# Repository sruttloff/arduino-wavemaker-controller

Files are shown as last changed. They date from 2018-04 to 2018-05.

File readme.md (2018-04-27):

2 Jebao Wavemaker (SW-4) Pumpen selbst steuern
=======
Da das Strömungsbild trotz der vielen Möglichkeiten die die Controller von Hause aus bieten, nicht meinen Wünschen entsprach, habe ich dieses kleine Projekt auf die Beine gestellt.
Über die PWM Pins des Arduino wird ein Signal erzeugt und mit einem RC-Glied in eine Gleichspannung umgewandelt.
Die Gleichspannung wird über den OP verstärkt und liefert am OP Ausgang 0-9V (oder 0-10V wenn man eine 10V Spannungsquelle hat).
Im Programm wird Pump1 als Master betrachtet und Pumpe 2 ist Slave. Wenn Pump1 auf 100% läuft, läuft Pumpe2 mit 0%.
Es gibt 4 Timings (siehe Bild) die man frei definieren kann. Auch sind 0% und 100% Leistung frei einstellbar (PWM Rate 0-255).
0% bedeutet bei mir, dass die Pumpe mit minimaler Leistung läuft, so dass diese gerade nicht stehen bleibt.
Den Arduino Sketch also einfach im Kopfteil an die eigenen Bedürfnisse anpassen.

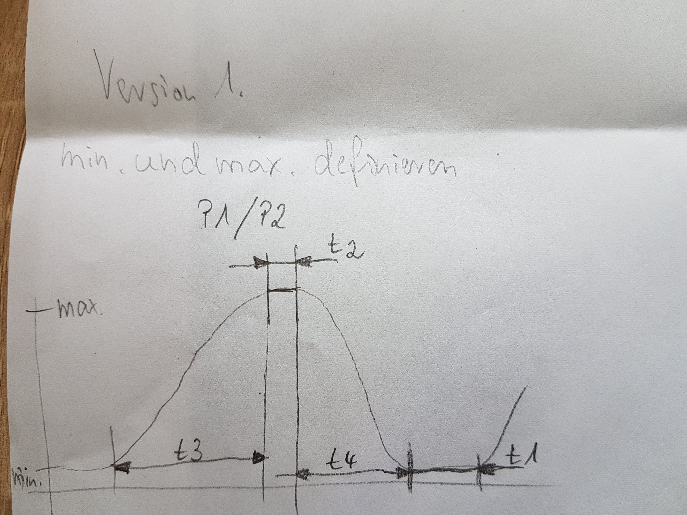
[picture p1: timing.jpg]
Timing Diagramm


Zur Umsetzung benötigt wird:
1. Arduino Mega 2560 (eine kleinere Version des Arduino tut's auch, dann muss allerdings die Pinbelegung angepasst werden)
2. 1 x OP Verstärker LM358
3. 6 x 10kOhm Widerstände
4. 2 x 22uF Elko's
5. Netzteil mit 9-12V DC
6. Ein paar Meter 2 Adriges Kabel + Hohlstecker (3,5mm / 1,45mm) um die Controller der Pumpen anzuschliessen.

Hier der Schaltplan:
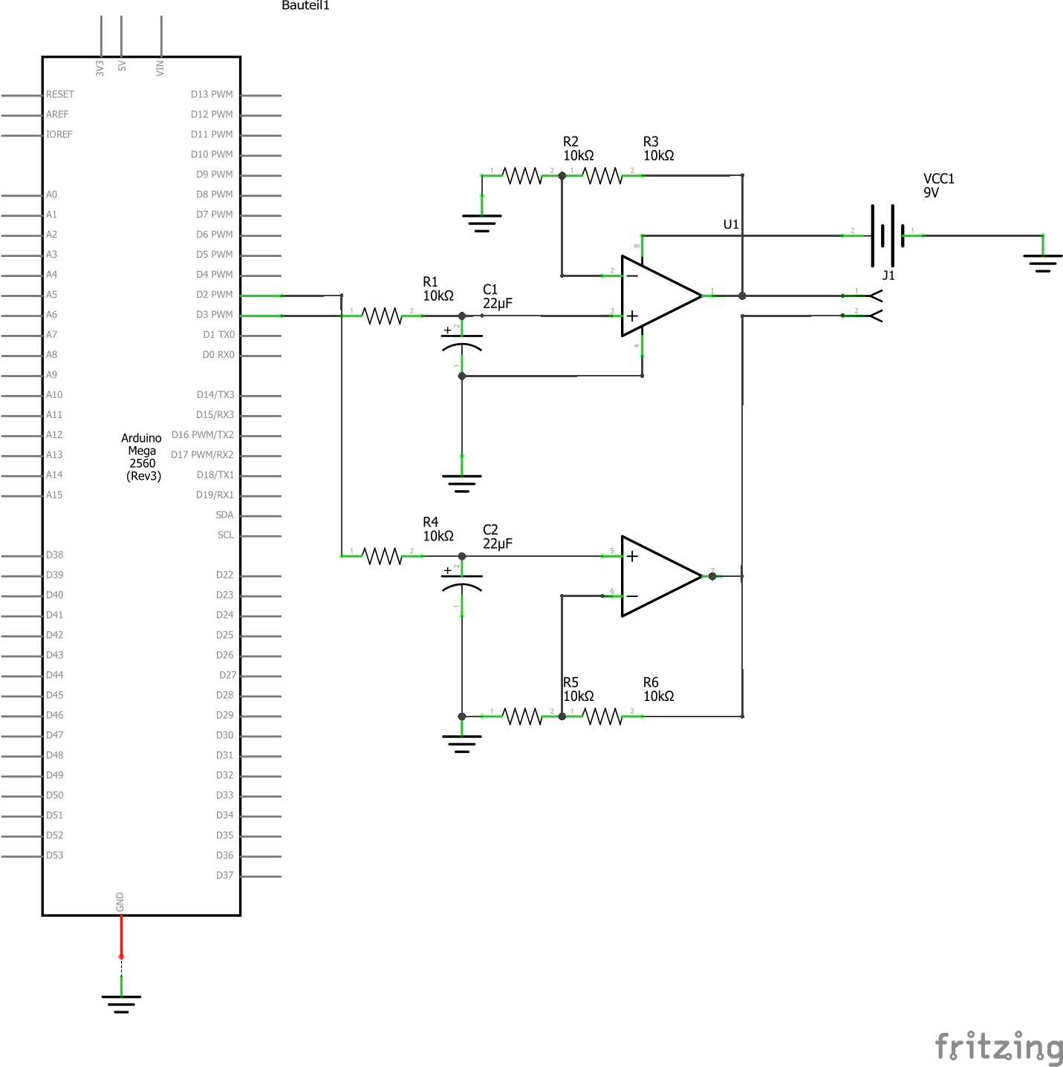
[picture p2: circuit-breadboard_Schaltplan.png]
Schaltplan


Hier der Aufbau auf einer Steckplatine (Breadboard):
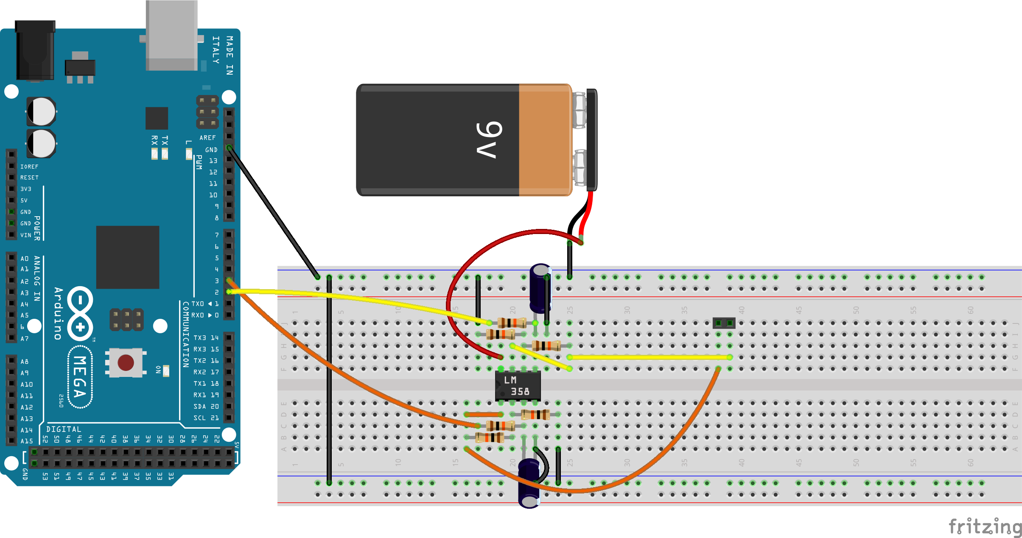
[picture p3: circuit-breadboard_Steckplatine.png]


Die Pin 1 und 2 von J1 liefern dann die Spannung von 0-9V für die beiden Controller.
Ich selbst habe die SW-4 Controller mit Hohlsteckern angeschlossen.
Hat man die Version der Controller ohne die Steckanschlüsse, muss man das Gehäuse öffnen. Einfach die 4 Schrauben auf der Rückseite entfernen.
Dann den Deckel abnehmen. Nun muss die Platine gelöst werden. An der Stelle wo eigentlich die Buchse sitzen sollte, wurde vom Hersteller der Ground-Pin mit dem Kontaktpin der Buchse verlötet.
Entweder ist da nur sehr viel Lötzinn drauf oder ein Draht wurde zwischengelötet. Das muss man entfernen.
Der Nachteil ist hierbei, dass der Controller nun nichts mehr tut, da er auf ein Signal von aussen wartet. 
Einen Kippschalter aufzulöten, bringt die Lösung. So kann man zwischen normalem und externem Modus umschalten.

Hier ein Foto wo man den Draht anlötet:
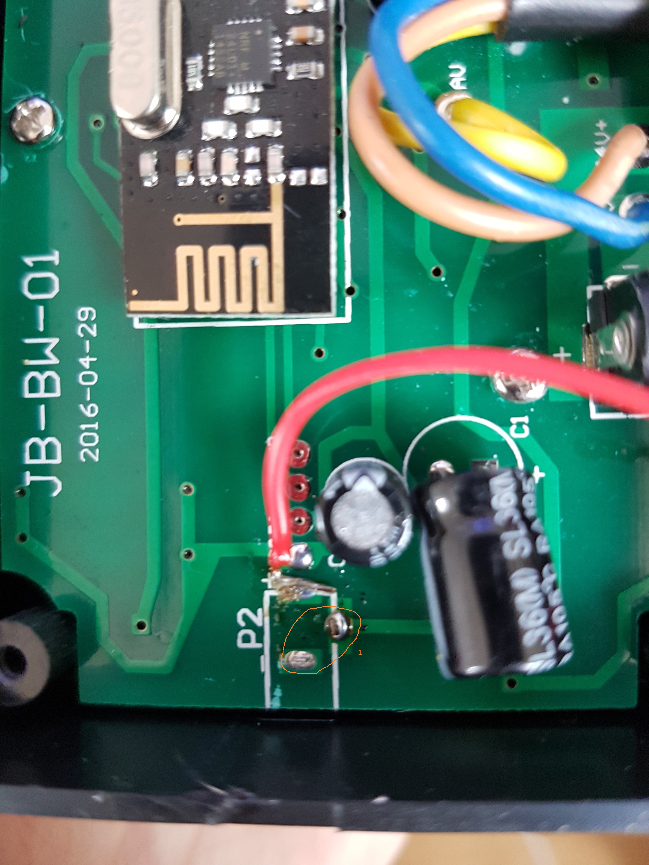
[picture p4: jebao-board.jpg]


Markierung 1 zeigt, wo die Brücke auf der Vorderseite der Platine zu entfernen ist. Statt der Brücke einen Schalter zwischen setzen.
An den - kommt dann der Minus von der Schaltung und an + der Ausgang von der Schaltung.

Optionaler Schalter zur Fütterung
Bei Drücken des Schalters wird der Fütterungsmodus aktiviert. Die Pumpen stehen für 10 Sekunden still.
Erneutes Drücken, bricht den Modus ab.
Hier der Schaltplan und der Aufbau auf einer Steckplatine (Breadboard)::
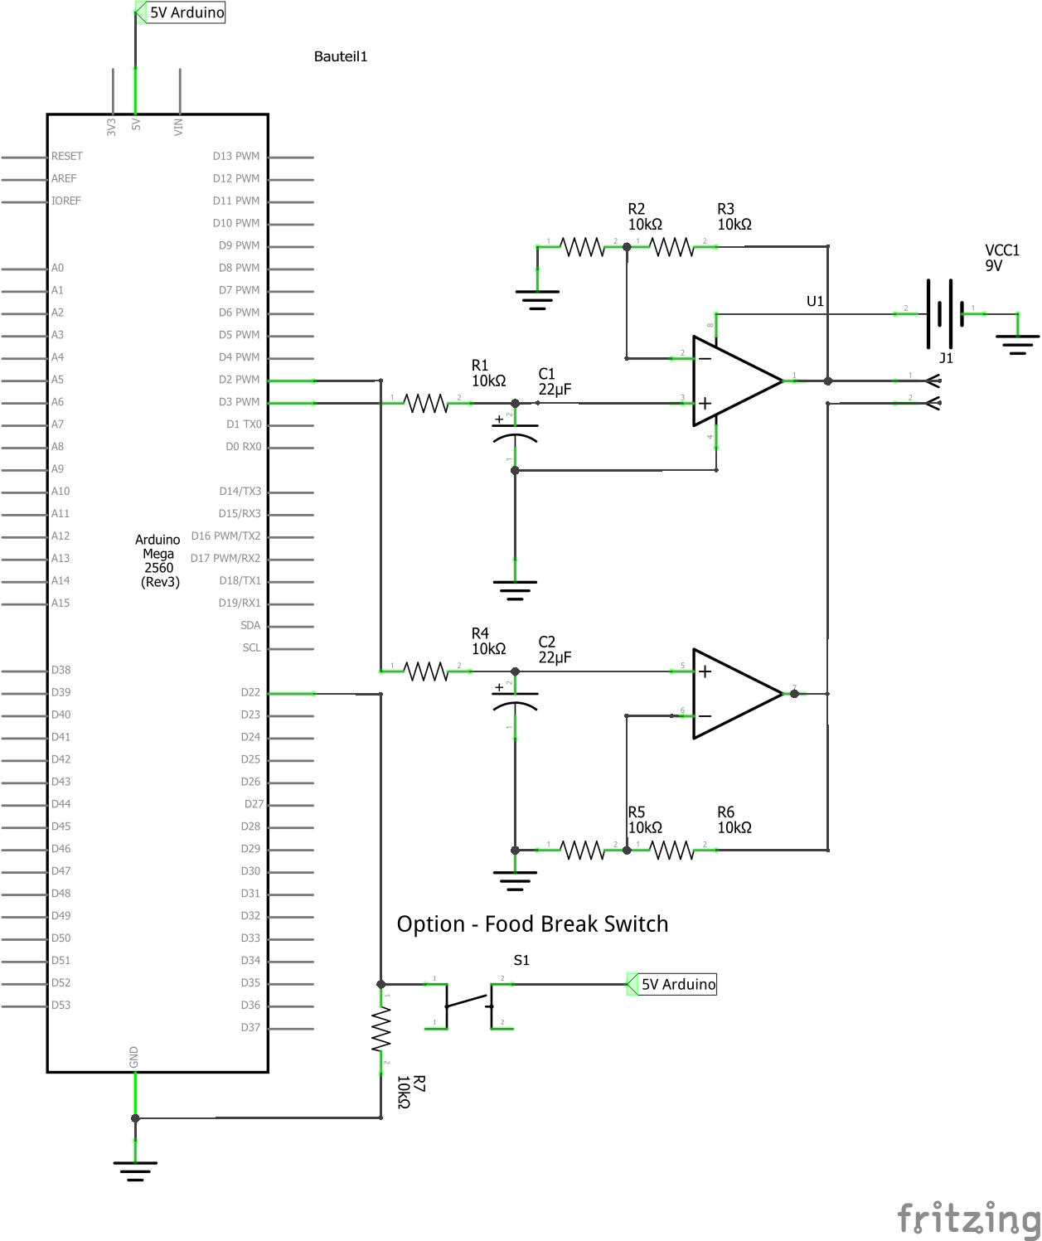
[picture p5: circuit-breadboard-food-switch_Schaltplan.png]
Schaltplan


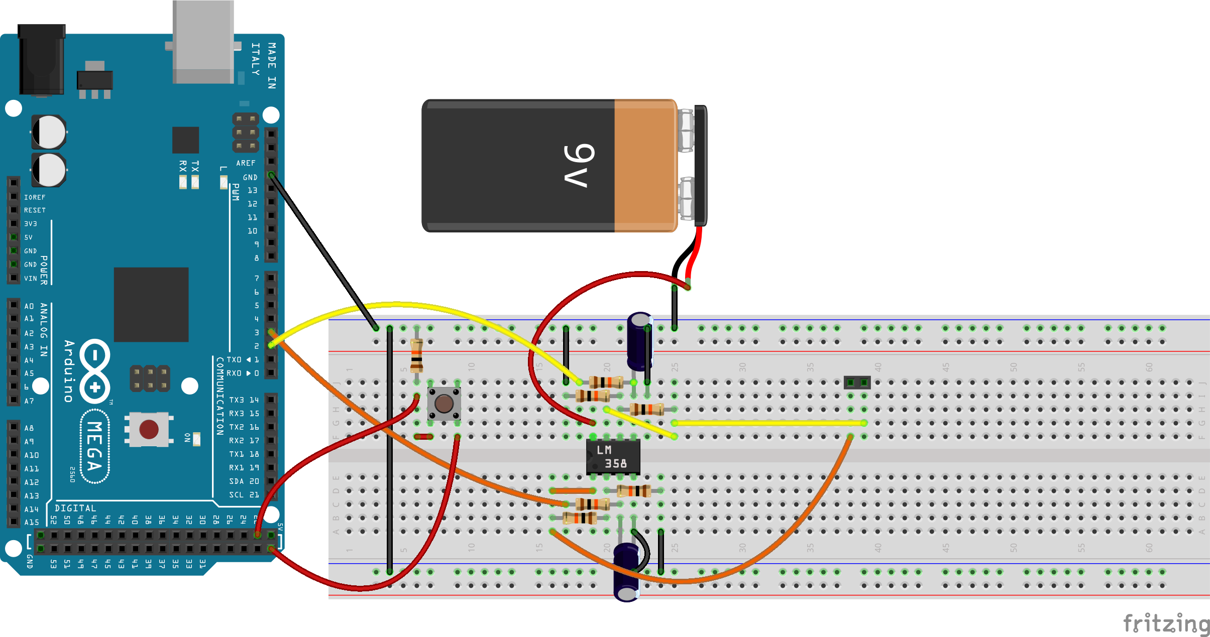
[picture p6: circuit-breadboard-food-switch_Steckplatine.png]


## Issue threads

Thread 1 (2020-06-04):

nRF24 protocol

martinhladil, 2020-06-04:
Very nice project to control the pump in an analog way. Thanks for that!

However, have you ever thought about controlling it via nRF24 which is on board? This is the way how master controller speaks to slave controllers wirelessly. I'm thinking about cracking it by myself, I'm just curious if you maybe did some progress here as well.

sruttloff, 2020-06-04:
Thank you for your interest.
No, I did not want to implement this via the slave function (radio). Quite simply to be able to use other controllers with 10V input at a later time.
The Jebao pumps have now also been replaced and it was sufficient to produce a suitable cable.

Closed 2020-06-04.

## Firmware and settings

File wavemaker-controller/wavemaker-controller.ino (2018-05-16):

/*
  Jebao SW Wavemaker Controller with Arduino Mega

  Does controll 2 Wavemaker controller (0-10V DC). One is master, the other is slave and runs reversed against No.1
  Food Button can be connected optionally.  

  Free for all!
 */

#include <Arduino.h>
extern HardwareSerial Serial;

int pump1 = 3; // the PWM pin the right pump is attached to
int pump2 = 4; // the PWM pin the left pump is attached to
int pump1Min = 45; //45 ist der kleinste
int pump1Max = 235;
int pump2Min = 45;
int pump2Max = 255;
int pump1Current = 0, pump2Current = 0;
int t1 = 30; // time in secs. to stay at level min
int t2 = 30; // time in secs. to stay at max
int t3 = 15; // time in secs. to go from min to max
int t4 = 15; // time in secs. to go from max to min

/*
 * timer 1 = for wavemaker timing
 * timer 5 = food timer
 */
const int timerElements = 5; // qty of timer's to init
unsigned long timerArray[timerElements + 1];
unsigned long tempTime[timerElements + 1]; // needed to calculate progress
String step = "t1"; // step marker
float myTimer(int timerNo = 0, long time = 0);
void setPump1Speed(float rate);
void setPump2Speed(float rate);
void pumpMaster();
int foodBreak = 0;
long foodTime = 600; // food time in secs.
int foodSwitch = 22;
int tmpSwitch = 0;
float tmpFood = 0;

void setup() {
    pinMode(pump1, pump1Current);
    pinMode(pump2, pump2Current);
    Serial.begin(9600);
    // init timer array  
    for (int i = 0; i < timerElements; i++) {
        timerArray[i] = 0;
        tempTime[i] = 0;
    }
    pinMode(foodSwitch, INPUT);
    digitalWrite(foodSwitch, HIGH);
    setPump1Speed(50.0);
    delay(500);
}

void foodSwitchAction() {
    int digitalVal = digitalRead(foodSwitch);
    // switch pressed
    if (!tmpSwitch && HIGH == digitalVal)
        tmpSwitch = 1;
    // switch released
    if (tmpSwitch && LOW == digitalVal) {
        tmpSwitch = 0;
        if (foodBreak == 1) {
            // make timer run out of time
            Serial.println("Switch Pressed and released to stop timer");
            myTimer(5, (long) 1);
        } else {
            foodBreak = 1;
            analogWrite(pump1, 0);
            analogWrite(pump2, 0);
            // start food timer
            foodTime = (long) foodTime * (long) 1000;
            Serial.println("Switch Pressed and released " + String(foodTime));
            myTimer(5, (long) foodTime);
        }
    }
    if (foodBreak == 1) {
        float tmp = myTimer(5);
        if (tmpFood < tmp) {
            tmpFood = ceil(tmp);
            Serial.println("Food Timer at " + String(tmpFood) + "%");
        }
        // timer reached      
        if (tmp >= 100.00) {
            foodBreak = pump1Current = pump2Current = 0;
            step = "t1";
            myTimer(5, -1); // reset Timer
            myTimer(1, -1); // reset pump Timer
            setPump1Speed(50.0);
            delay(700);
            Serial.println("Food end");
        }
    }
}

void loop() {
    if (!foodBreak)
        pumpMaster();
    foodSwitchAction();
    test();
}
void setPump1Speed(float rate) {
    // rate is percent
    int tmpRange = pump1Max - pump1Min;
    if (rate < 0.00)
        rate = 0.00;
    if (rate > 100.00)
        rate = 100.00;
    int speed = (float) pump1Min + (tmpRange * (rate / 100.00));
    // set new speed when not already set
    if ((int) speed != pump1Current) {
        //    if (rate <= 2.00 || rate >= 98.00)
        //      Serial.println("Pump 1 at Rate: " + String(rate) + "% Value: " + String((int)speed));
        pump1Current = (int) speed;
        analogWrite(pump1, pump1Current);
        setPump2Speed((float) 100.00 - rate);
    }
}

void setPump2Speed(float rate) {
    // rate is percent
    int tmpRange = pump2Max - pump2Min;
    if (rate < 0.00)
        rate = 0.00;
    if (rate > 100.00)
        rate = 100.00;
    int speed = (float) pump2Min + (tmpRange * (rate / 100.00));
    // set new speed when not already set
    if ((int) speed != pump2Current) {
        //    if (rate <= 1.00 || rate >= 99.00)
        //      Serial.println("Pump 1 at Rate: " + String(rate) + " Value: " + String((int)speed));
        pump2Current = (int) speed;
        analogWrite(pump2, pump2Current);
    }
}

void pumpMaster() {
    // go to min
    if (step == "t4") {
        if (myTimer(1) == 0.0) {
            Serial.println("Decrease to min");
            myTimer(1, t4 * 1000);
        }
        // set pump speed            
        float tmp = myTimer(1);
        float speed = 100.00 - tmp;
        setPump1Speed(speed);
        if (tmp >= 100.00) {
            setPump1Speed(0.00);
            step = "t1";
            Serial.println("Decrease to min finished");
            myTimer(1, -1); // reset Timer
        }
    }
    // go to max
    if (step == "t3") {
        if (myTimer(1) == 0.0) {
            Serial.println("Grow to max");
            myTimer(1, t3 * 1000);
        }
        // set pump speed
        float speed = myTimer(1);
        setPump1Speed(speed);
        //Serial.println("Speed: " + String(speed) + " - " + String(speed * log10(speed)) + " test = " + String((speed * log10(speed)) - speed));
        if (myTimer(1) >= 100.00) {
            setPump1Speed(100.00);
            step = "t2";
            Serial.println("Grow to max finished");
            myTimer(1, -1); // reset Timer
        }
    }
    // keep at min
    if (step == "t1") {
        //Serial.println("myTimer(1)=" + String(myTimer(1)));   
        if (myTimer(1) == 0.0) {
            Serial.println("");
            Serial.println("");
            Serial.println("Stay at min");
            myTimer(1, t1 * 1000);
            setPump1Speed(0.00);
        }
        // timer reached      
        if (myTimer(1) >= 100.00) {
            step = "t3"; // t3
            myTimer(1, -1); // reset Timer
        }
    }
    // keep at max
    if (step == "t2") {
        if (myTimer(1) == 0.0) {
            Serial.println("Stay at max");
            myTimer(1, t2 * 1000);
            setPump1Speed(100.00);
        }
        // timer reached      
        if (myTimer(1) >= 100.00) {
            step = "t4";
            myTimer(1, -1); // reset Timer
        }
    }
}

// returns a percent value of time thats over or false if timer is run out
float myTimer(int timerNo, long time) {
    unsigned long tmpMillis = millis();
    // Serial.println("Timer " + String(timerNo) + " to time = " + String(time));
    if (time == (long) - 1) {
        timerArray[timerNo] = 0;
        tempTime[timerNo] = 0;
        Serial.println("Reset Timer " + String(timerNo) + " to time = " + String(time) + " Result in timerArray[timerNo] = " + String(timerArray[timerNo]));
    }
    if (time > (long) 0) {
        timerArray[timerNo] = tmpMillis + time;
        tempTime[timerNo] = time;
        Serial.println("Init Timer " + String(timerNo) + " to " + String(time) + " Result in timerArray[timerNo] = " + String(timerArray[timerNo]));
    }
    if (tempTime[timerNo] <= 0)
        return 0.0;

    unsigned long diff = (timerArray[timerNo] - tmpMillis);
    //   Serial.println("diff " + String(diff) + " = " + "(" + String(timerArray[timerNo]) + " - " + String(tmpMillis) + ")");
    float progress = float(100) - ((float) 100 / (float) tempTime[timerNo] * (float) diff);
    //Serial.println("Progress " + String(progress) + "%");
    if (timerArray[timerNo] > 0 && timerArray[timerNo] <= tmpMillis) {
        //Serial.println("Timer " + String(timerNo) + " is run out because: " + String(timerArray[timerNo]) + " <= " + String(tmpMillis));        
        return 100.00;
    } else
        return progress;
}
